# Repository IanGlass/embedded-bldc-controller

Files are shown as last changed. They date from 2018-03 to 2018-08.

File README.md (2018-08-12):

# Embedded-BLDC-Controller

This project contains a embedded microcontroller project to convert an input analogue voltage into an out PWM to drive a Hyperion BLDC controller.

## Circuit Schematic
The schematic contains three main modules:
* A TPS78001 voltage regulator to supply, configured with a 1M and 536 k resistor combination to provide a steady 3.5 V power source.
* A program header to interface to a J-Link LITE CortexM via SWD for flashing and debugging using Simplicity Studio.
* An EFM32TG microcontroller with an external oscillator.

The *Drive* pin is the analgoue input for the device, where the resistor (*R3* & *R4*) pair is currently configured to scale a 12 V input range to a 3.5 V input range. These can be altered to accommodate different inputs.

<p align="center">
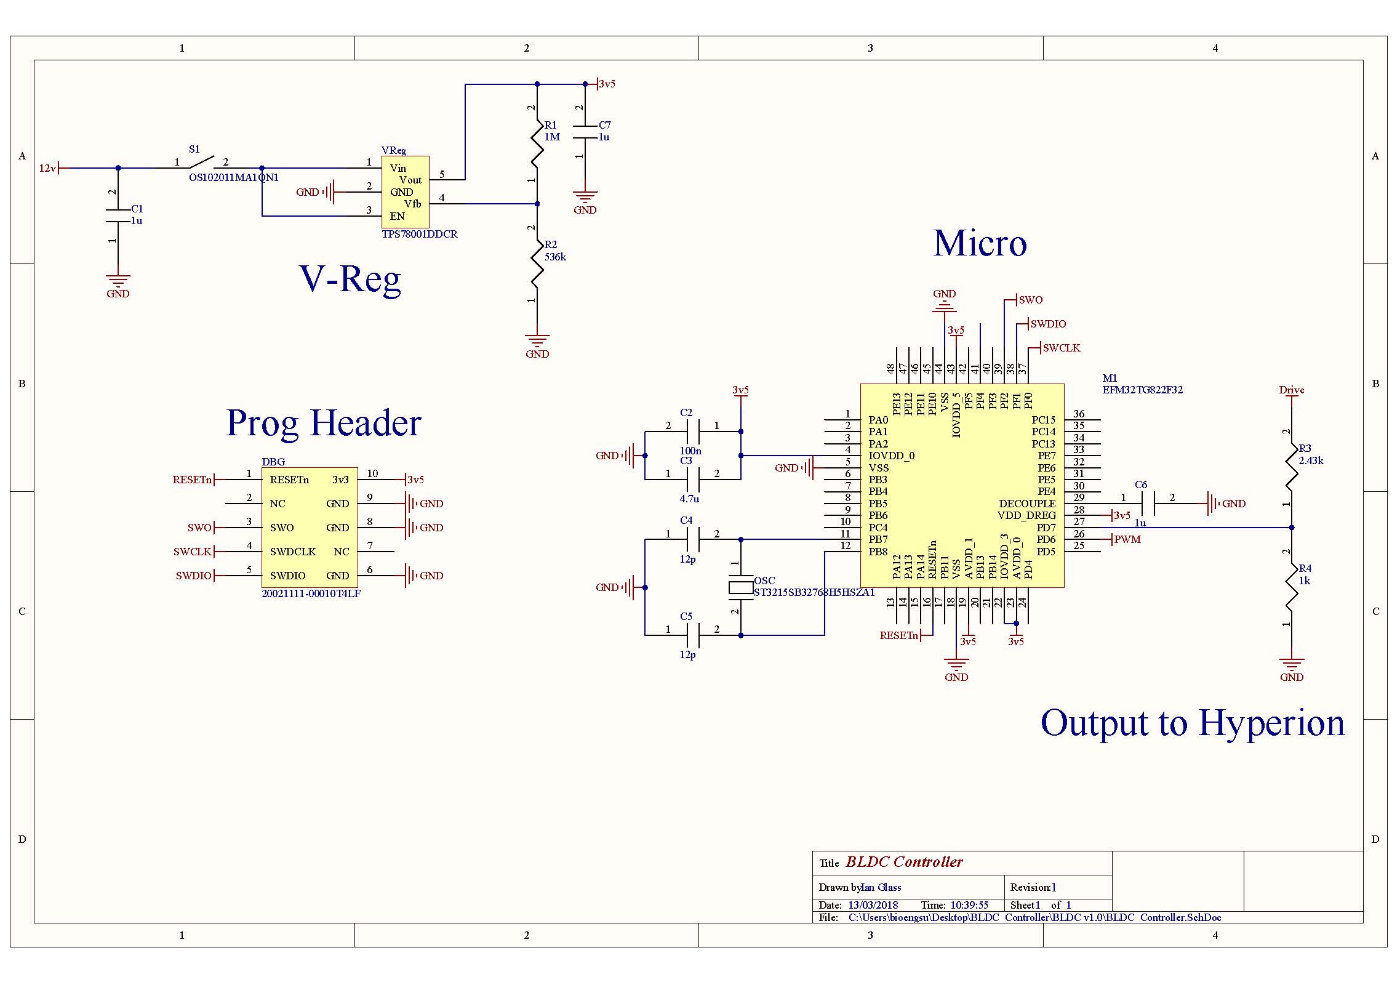
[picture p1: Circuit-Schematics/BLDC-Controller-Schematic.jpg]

</p>

## Code

Before normal operation commences, the Hyperion controller requires a 10% PWM with a 20 ms period to be driven for 2 seconds. This is a built in safety feature with Hyperion. After successful initialisation, the Hyperion controller will make a few short beeps to indicate success. Normal PWM operation is commenced by enabling the Timer0 IRQ via *NVIC_EnableIRQ(TIMER0_IRQn)*.
```c
/*-----------------------------------------------------------*/
/**
  * @brief Function used to initialise the Hyperion BLDC, which expects
  * a predefined sequence before being driveable. Start with 
  * 2ms high PWM on 20ms wave period for 2 secs
  * @param  None
  * @retval None
  */
void InitialiseHyperion(void) {
	int StartupCounter = 0;
	/* Drive BLDC at full speed */
	while (StartupCounter < StartupStop) {
		/* If PWM pin low */
		if (GPIO_PinInGet(PWM_PORT, PWM_PIN)) {
			GPIO_PinOutClear(PWM_PORT, PWM_PIN);
			/* Drive low for 18 ms */
			Delay(18);
		}
		/* Drive PWM pin high */
		else {
			GPIO_PinOutSet(PWM_PORT, PWM_PIN);
			/* Drive high for 2 ms */
			Delay(2);
		}
		StartupCounter++;
	}
	/* Enable TIMER0 Interrupt vector in NVIC, begins normal PWM operation */
	NVIC_EnableIRQ(TIMER0_IRQn);
}
```

The ADC peripheral is constantly polled in background to retrieve ADC values via the *Drive* input pin. The *SampleADC()* function takes a wait parameter which specifies the time to wait for a conversion to complete using a blocking wait function. The function then grabs the ADC value and scales it against 4,095 which is the maximum ADC register value (or 3.6 V). The function returns the scaled value to a global *Speed* value used for PWM.
```c
/*-----------------------------------------------------------*/
/**
  * @brief Performs a single acquisition of the ADC pin. This is
  * the input to specify the drive output.
  * @param  Length to wait for the ADC conversion (ms)
  * @retval The scaled PWM drive time
  */
uint32_t SampleADC(int wait) {
	uint32_t ADCVal;
	/* Request ADC sample */
	ADC_Start(ADC0, adcStartSingle);
	/* Wait for conversion, needs to be replaced with wait function to 
	* check for ADC conversion complete */
	Delay(wait);
	/* Grab register value */
	ADCVal = ADC_DataSingleGet(ADC0);
	/* Scale input voltage as a percentage of 3.6V max expected at voltage 
	* divided input */
	return ADCVal*100/4095;
}
```

The Timer0 IRQ performs PWM of the Hyperion controller using the previously calculated *Speed* variable to set the PWM duty cycle. PWM has a period of 20 ms, which is what the Hyperion controller expects.
```c
/*-----------------------------------------------------------*/
/**
  * @brief Timer0 ISR to drive PWM pin based on Speed set by
  * SampleADC() function.
  * @param  None
  * @retval None
  */
void TIMER0_IRQHandler(void) {
	//Clear overflow interrupt flag
	TIMER_IntClear(TIMER0, TIMER_IF_OF);
	//Drive range is 1-2ms so first 1ms is mandatory. Full wave is 20ms
	if (PWMTime < (Offset + Speed)) {
		GPIO_PinOutSet(PWM_PORT, PWM_PIN);
	}
	else {
		GPIO_PinOutClear(PWM_PORT, PWM_PIN);
	}
	PWMTime++;
	if (PWMTime > 2000) {
		PWMTime = 0;
	}
}
```

## Setup

The drive input and output pins are designated with "Drive" and "PWM" respectively. The input and output wires can be soldered to these through-hole pads. The setup with a hyperion controller is shown.

<p align="center">
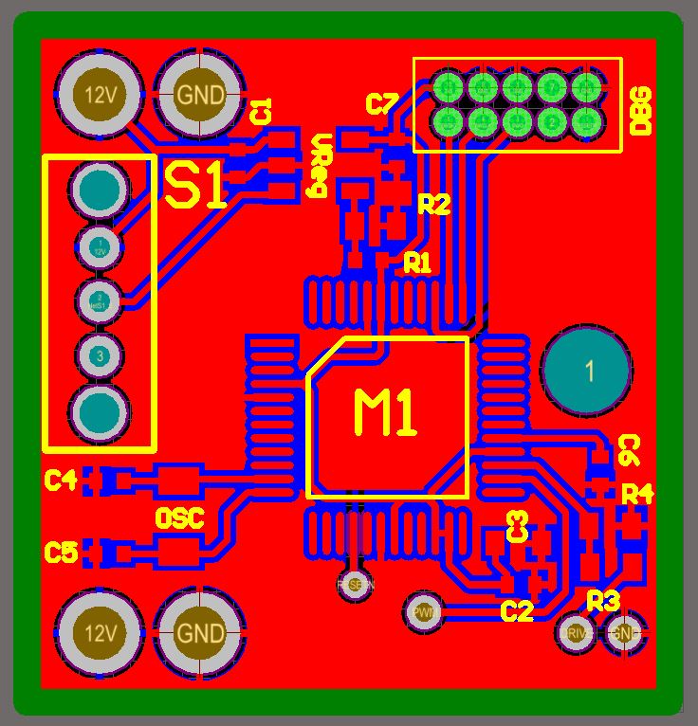
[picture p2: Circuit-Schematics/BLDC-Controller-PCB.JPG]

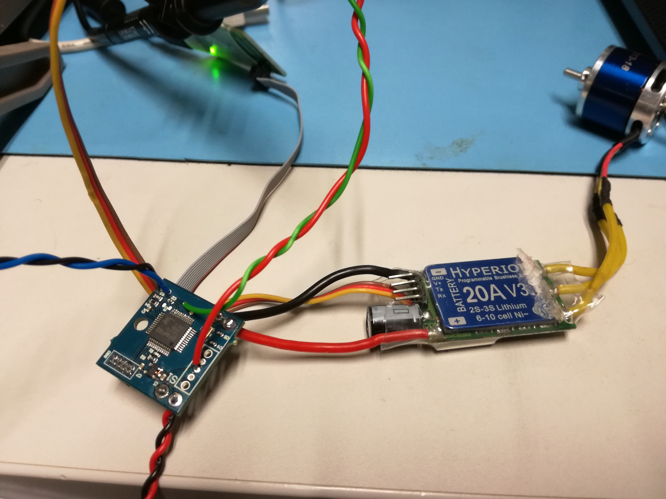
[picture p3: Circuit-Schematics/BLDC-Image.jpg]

</p>

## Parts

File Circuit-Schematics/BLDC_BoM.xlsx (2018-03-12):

Part type | Part number | Manufacturer Part Number | Supplier | Quantity | Unit Price | Total Price
MCU | 904-EFM32TG822F32T | EFM32TG822F32-QFP48T | Mouser | 1 | 4.16 | 4.16
V Reg | 595-TPS78001DDCR | TPS78001DDCR | Mouser | 1 | 1.61 | 1.61
Switch | 611-OS102011MA1QN1 | OS102011MA1QN1 | Mouser | 1 | 0.63 | 0.63
Osc | 581-ST3215SB3H5HSZA1 | ST3215SB32768H5HSZA1 | Mouser | 1 | 1.28 | 1.28
Cap 12p | 581-04025A120J | 04025A120JAT2A | Mouser | 2 | 0.268 | 0.536
Cap 4.7u | 81-GRM035R60J475ME5D | GRM035R60J475ME15D | Mouser | 1 | 0.961 | 0.961
Cap 100n | 77-VJ0402V104ZXJCBC | VJ0402V104ZXJCW1BC | Mouser | 1 | 0.11 | 0.11
Cap 1u | 710-885012106017 | 885012106017 | Mouser | 3 | 0.158 | 0.474
Res 1M | 71-CRCW0402-1.0M-E3 | CRCW04021M00FKED | Mouser | 1 | 0.158 | 0.158
Res 536k | 603-RC0603FR-07536KL | RC0603FR-07536KL | Mouser | 1 | 0.158 | 0.158
Res 1k | 667-ERJ-P03F1001V | ERJ-P03F1001V | Mouser | 1 | 0.599 | 0.599
Res 2.43k | 603-RC0603FR-072K43L | RC0603FR-072K43L | Mouser | 1 | 0.158 | 0.158
DBG | 649-221111-00010T4LF | 20021111-00010T4LF | Mouser | 1 | 1.01 | 1.01
Heat sink | 532-577102B00 | 577102B00000G | Mouser | 1 | 0.457 | 0.457
 |  |  |  | 17 |  | 12.301

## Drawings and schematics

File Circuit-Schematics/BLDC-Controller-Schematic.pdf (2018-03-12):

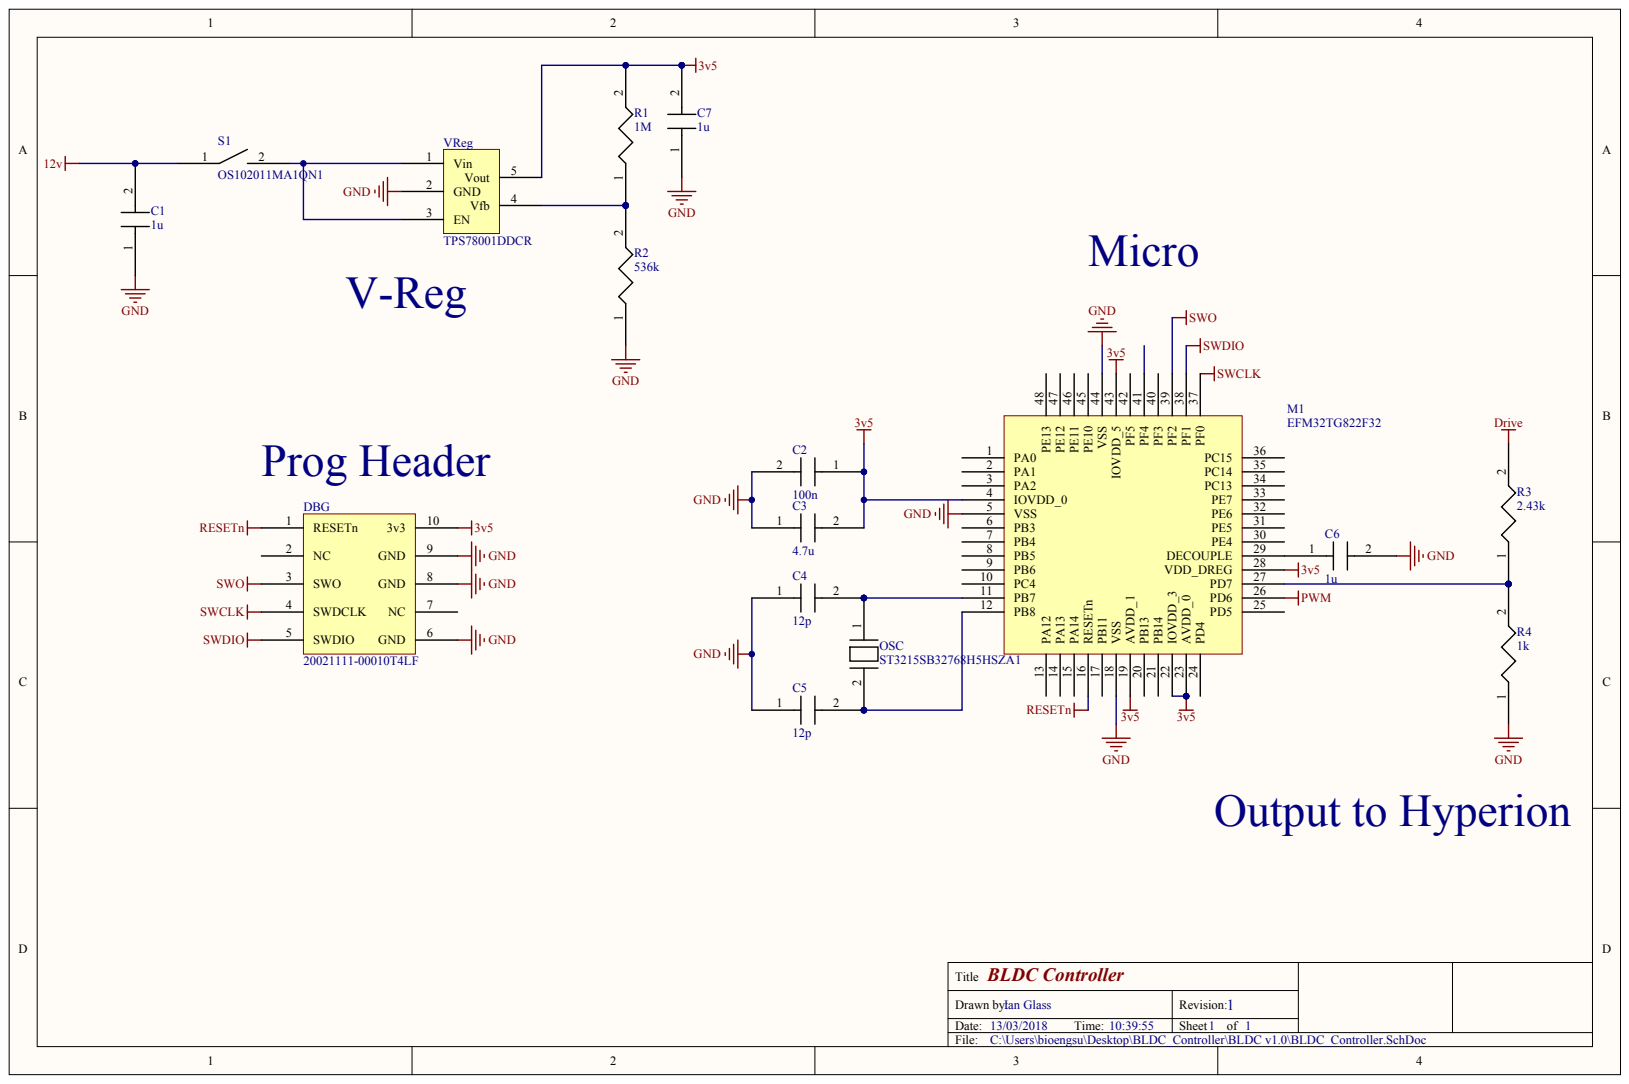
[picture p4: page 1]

BLDC Controller Title

Drawn by: Ian Glass | Revision: 1

Date: 13/03/2018 Time: 10:39:55 | Sheet 1 of 1

C:\Users\bioengsu\Desktop\BLDC_Controller\BLDC v1.0\BLDC_Controller.SchDoc

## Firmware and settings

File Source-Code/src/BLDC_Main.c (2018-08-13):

/**************************************************************************//**
* @file BLDC_Main.c
* @author Ian Glass
* @version 3.20.2
* @date    28-July-2018
* @brief   Main module for the BLDC driver
*******************************************************************************
*
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
*******************************************************************************/

/* Includes ------------------------------------------------------------------*/
#include <stdint.h>
#include <stdbool.h>
#include <stdio.h>

#include "em_device.h"
#include "em_chip.h"
#include "em_gpio.h"
#include "em_cmu.h"
#include "em_timer.h"
#include "em_int.h"
#include "em_adc.h"

/* Global Variables ----------------------------------------------------------*/
int PWMTime;
uint32_t Speed = 0;
int Timer = 0;

/*-----------------------------------------------------------*/
/**
  * @brief Interrupt Service Routine for system tick counter, 1 ms 
  * call period, increments a globally accessible Timer variable 
  * for the Delay() function.
  * @param  None
  * @retval None
  */
void SysTick_Handler(void) {
	Timer++;
}

/*-----------------------------------------------------------*/
/**
  * @brief Timer0 ISR to drive PWM pin based on Speed set by
  * SampleADC() function.
  * @param  None
  * @retval None
  */
void TIMER0_IRQHandler(void) {
	//Clear overflow interrupt flag
	TIMER_IntClear(TIMER0, TIMER_IF_OF);
	//Drive range is 1-2ms so first 1ms is mandatory. Full wave is 20ms
	if (PWMTime < (Offset + Speed)) {
		GPIO_PinOutSet(PWM_PORT, PWM_PIN);
	}
	else {
		GPIO_PinOutClear(PWM_PORT, PWM_PIN);
	}
	PWMTime++;
	if (PWMTime > 2000) {
		PWMTime = 0;
	}
}

/*-----------------------------------------------------------*/
/**
  * @brief Simple hard lock wait function.
  * @param  milliseconds to hard lock for
  * @retval None
  */
void Delay(int milliseconds) {
	//Reset global time increment
	Timer = 0;
	//Hard lock wait
	while (Timer < milliseconds);
}

/*-----------------------------------------------------------*/
/**
  * @brief Function used to initialise the Hyperion BLDC, which expects
  * a predefined sequence before being driveable. Start with 
  * 2ms high PWM on 20ms wave period for 2 secs
  * @param  None
  * @retval None
  */
void InitialiseHyperion(void) {
	int StartupCounter = 0;
	/* Drive BLDC at full speed */
	while (StartupCounter < StartupStop) {
		/* If PWM pin low */
		if (GPIO_PinInGet(PWM_PORT, PWM_PIN)) {
			GPIO_PinOutClear(PWM_PORT, PWM_PIN);
			/* Drive low for 18 ms */
			Delay(18);
		}
		/* Drive PWM pin high */
		else {
			GPIO_PinOutSet(PWM_PORT, PWM_PIN);
			/* Drive high for 2 ms */
			Delay(2);
		}
		StartupCounter++;
	}
	/* Enable TIMER0 Interrupt vector in NVIC, begins normal PWM operation */
	NVIC_EnableIRQ(TIMER0_IRQn);
}

/*-----------------------------------------------------------*/
/**
  * @brief ADC setup for PD7, the analogue input controls the
  *  BLDC drive speed
  * @param  None
  * @retval None
  */
void InitADC(void) {
	/* Enable clock for ADC0 peripheral */
	CMU_ClockEnable(cmuClock_ADC0, true);
	/* Initialiser structure for ADC0 peripheral using channel 7 */
	ADC_InitSingle_TypeDef ADCInit0 =
	{
		.prsSel = adcPRSSELCh0,
		.acqTime = adcAcqTime1,
		.reference = _ADC_SINGLECTRL_REF_VDD,
		.resolution = adcRes12Bit,
		.input = adcSingleInpCh7,
		.diff = false,
		.prsEnable = false,
		.leftAdjust = false,
		.rep = false,
	};
	/* Enable ADC module */
	ADC_InitSingle(ADC0, &ADCInit0);
}

/*-----------------------------------------------------------*/
/**
  * @brief Initialise PD6 GPIO and Timer for use as PWM driver
  * @param  None
  * @retval None
  */
void InitPWM(void) {
	/* Enables GPIO peripheral clocking */
	CMU_ClockEnable(cmuClock_GPIO, true);
	/* Set PWM pin to output with low state */
	GPIO_PinModeSet(PWM_PORT, PWM_PIN, gpioModePushPull, 0);
	/* Enable clock for TIMER0 peripheral */
	CMU_ClockEnable(cmuClock_TIMER0, true);
	/* Set TIMER0 overflow value, defines PWM output frequency */
	TIMER_TopSet(TIMER0, CMU_ClockFreqGet(cmuClock_HFPER)/PWM_FREQ);
	/* Construct TIMER0 initialiser structure */
	TIMER_Init_TypeDef timerInit0 =
	{
		.enable = true,
		.debugRun = true,
		.prescale = timerPrescale16,
		.clkSel = timerClkSelHFPerClk,
		.fallAction = timerInputActionNone,
	  	.riseAction = timerInputActionNone,
	  	.mode = timerModeUp,
	  	.dmaClrAct = false,
	  	.quadModeX4 = false,
	  	.oneShot = false,
	  	.sync = false,
	};
	/* Enable overflow interrupt flag */
	TIMER_IntEnable(TIMER0, TIMER_IF_OF);
	/* Configure timer, start normal operation */
	TIMER_Init(TIMER0, &timerInit0);
}

/*-----------------------------------------------------------*/
/**
  * @brief Performs a single acquisition of the ADC pin. This is
  * the input to specify the drive output.
  * @param  Length to wait for the ADC conversion (ms)
  * @retval The scaled PWM drive time
  */
uint32_t SampleADC(int wait) {
	uint32_t ADCVal;
	/* Request ADC sample */
	ADC_Start(ADC0, adcStartSingle);
	/* Wait for conversion to complete */
	Delay(wait);
	/* Grab register value */
	ADCVal = ADC_DataSingleGet(ADC0);
	/* Scale input voltage as a percentage of 3.6V max expected at voltage 
	* divided input */
	return ADCVal*100/4095;
}

/*-----------------------------------------------------------*/
/**
  * @brief Main function
  * @param None
  * @retval None
  */
int main(void)
{
  /* Chip errata */
  CHIP_Init();
  /* Setup Systick timer for 1mS interrupts */
  if (SysTick_Config(CMU_ClockFreqGet(cmuClock_CORE)/SYS_FREQ)) while (1);
  InitADC();
  InitPWM();
  /* Run function to initialise Hyperion BLDC controller */
  InitialiseHyperion();
  /* Globally enable interrupts, begins normal operation */
  INT_Enable();

  /* Background loop */
  while (1) {
	  /* ADC sample, wait in milliseconds as argument */
	  Speed = SampleADC(10);
  }
}
